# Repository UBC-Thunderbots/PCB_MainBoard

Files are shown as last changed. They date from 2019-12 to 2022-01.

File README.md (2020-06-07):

# PCB_MainBoard README

## Description

This repository contains Altium PCB files for UBC Thunderbots' main board pcb. Anyone who wishes to push changes to this project must get permission from the current Electrical Team Lead.

## Getting Started

### Required software

1. git
2. Altium Designer

### Instructions

1. Either create a new working branch or select an existing branch other than `master`.
2. **Recursively clone** (`git clone --recurse-submodules`) your working branch of the repository to your PC (i.e. `C:/Documents/thunderbots/PCB_MainBoard`).
3. In Altium Designer, navigate to *Preferences -> Data Management -> Version Control* and ensure **SVN - Subversion** is enabled and **Version 1.9** is selected.
4. In Altium Designer, navigate to *Preferences -> Data Management -> Design Repositories*.
5. Within *Design Repositories* click on on *Connect To* -> **SVN**.
6. In the dialogue box that comes up, fill in the following information:

Field|Selection/Input
---|---
Name|PCB_MainBoard
Default Checkout Path|location of local repository (i.e. `C:/Documents/thunderbots/PCB_MainBoard`)
Method|https
Server|github.com
Server Port|Default
Repository Subfolder|/UBC-Thunderbots/PCB_MainBoard
User Name|*your github login username*
Password|*your github login password*

7. Click **Test**.

After your repository is connected, you can add or remove files like a regular Altium Project folder and then commit and push your changes to the remote repository.

[Reference](https://forum.live.altium.com/#posts/235981/718003)

### Altium_Libraries Submodule Integration

To enforce component and board compatibility, the Altium_Libraries repository is integrated as a submodule. Before making changes to a project, **ensure that your local `Altium_Libraries/` submodule is current**. This can be done using `git submodule update` in git bash.

## Repository Structure

At the highest level, there should be the most up to date board revisions, (e.g.
`mainboard-v1.0/`), `archive/`, and `Altium_Libraries/`. Any previous versions should be placed in `archive/`. Every board revision directory should abide by the following structure:

```
<name-v#>/
├── doc/
│   ├── <name>.pdf
│   └── <name>.xslx or <name>.csv
├── pcb/
│   ├── guidelines/
│   ├── <name>.PrjPCB
│   ├── <name>.SchDoc
│   └── <name>.PcbDoc
└── sim/
```

### doc/

For documentation and relevant non-simulation and layout files. This includes PDFs of the design and bills of materials (`*.xlsx` or `.csv` format).

### pcb/

For any PCB design software files related to the schematic capture and PCB layout of board. This includes schematic and PCB layout guidelines (`guidelines/`).

### sim/

For any simulation files related to the PCB design here.

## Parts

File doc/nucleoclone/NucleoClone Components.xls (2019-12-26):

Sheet: Part List Report
Part List |  | Bill of Materials for Project [NucleoClone.PrjPcb] (No PCB Document Selected)
Source Data From: |  | NucleoClone.PrjPcb
Project: |  | NucleoClone.PrjPcb
Variant: |  | None
Report Date: | 12/19/2019 | 12:15 PM
Print Date: | 2019-12-19 | 12:15:50
Designator | Comment | LibRef | Footprint | Description
B1 | SW-PUSH-CMS | MCD-00002 | SWI_WEALTHMETAL_TD-0341_4P_BLUE | Non-Open Push-Button 0.1A 24V
B2 | SW-PUSH-CMS | MCD-00001 | SWI_WEALTHMETAL_TD-0341_4P_BLACK | Non-Open Push-Button 0.1A 24V BLACK
C38 | Capacitor | MCD-00006 | C0402 | Capacitor, MLCC, 100nF, 16V, X7R, 10%, 0402, T=0.5mm
C39 | Capacitor | MCD-01121 | C0603 | Capacitor, MLCC, 4.7µF, 10V, X5R, 20%, 0603, T=0,8mm
C40 | Capacitor | MCD-00097 | C0603 | Capacitor, MLCC, 4.7uF, 16V, X5R, 20%, 0603, T=0,8mm
C41 | Capacitor | MCD-00014 | C0805 | Capacitor, MLCC, 10uF, 25V, X5R, 10%, 0805, T=0,85mm
C42 | Capacitor | MCD-00014 | C0805 | Capacitor, MLCC, 10uF, 25V, X5R, 10%, 0805, T=0,85mm
C43 | Capacitor | MCD-00097 | C0603 | Capacitor, MLCC, 4.7uF, 16V, X5R, 20%, 0603, T=0,8mm
C44 | Capacitor | MCD-00237 | C0603 | Capacitor, MLCC, 100nF, 6V3, X5R, 10%, 0603, T=0,8mm
C45 | Capacitor | MCD-01121 | C0603 | Capacitor, MLCC, 4.7µF, 10V, X5R, 20%, 0603, T=0,8mm
C46 | Capacitor | MCD-01123 | C0402 | [obsolete] Capacitor, MLCC,100nF, 10V, X7R, 10%, 0402, T=0.5mm
C47 | Capacitor | MCD-01123 | C0402 | [obsolete] Capacitor, MLCC,100nF, 10V, X7R, 10%, 0402, T=0.5mm
C48 | Capacitor | MCD-00012 | C0603 | Capacitor, MLCC, 2.2uF, 10V, X5R, 10%, 0603, T=0,8mm
C49 | Capacitor | MCD-01123 | C0402 | [obsolete] Capacitor, MLCC,100nF, 10V, X7R, 10%, 0402, T=0.5mm
C50 | Capacitor | MCD-00012 | C0603 | Capacitor, MLCC, 2.2uF, 10V, X5R, 10%, 0603, T=0,8mm
C51 | Capacitor | MCD-01123 | C0402 | [obsolete] Capacitor, MLCC,100nF, 10V, X7R, 10%, 0402, T=0.5mm
C52 | Capacitor | MCD-01123 | C0402 | [obsolete] Capacitor, MLCC,100nF, 10V, X7R, 10%, 0402, T=0.5mm
C53 | Capacitor | MCD-01123 | C0402 | [obsolete] Capacitor, MLCC,100nF, 10V, X7R, 10%, 0402, T=0.5mm
C54 | Capacitor | MCD-01123 | C0402 | [obsolete] Capacitor, MLCC,100nF, 10V, X7R, 10%, 0402, T=0.5mm
C55 | Capacitor | MCD-01123 | C0402 | [obsolete] Capacitor, MLCC,100nF, 10V, X7R, 10%, 0402, T=0.5mm
C56 | Capacitor | MCD-01123 | C0402 | [obsolete] Capacitor, MLCC,100nF, 10V, X7R, 10%, 0402, T=0.5mm
C57 | Capacitor | MCD-01123 | C0402 | [obsolete] Capacitor, MLCC,100nF, 10V, X7R, 10%, 0402, T=0.5mm
C58 | Capacitor | MCD-01123 | C0402 | [obsolete] Capacitor, MLCC,100nF, 10V, X7R, 10%, 0402, T=0.5mm
C59 | Capacitor | MCD-00237 | C0603 | Capacitor, MLCC, 100nF, 6V3, X5R, 10%, 0603, T=0,8mm
C60 | Capacitor | MCD-01121 | C0603 | Capacitor, MLCC, 4.7µF, 10V, X5R, 20%, 0603, T=0,8mm
C61 | Capacitor | MCD-00238 | C0603 | Capacitor, MLCC, 1uF, 6V3, X5R, 10%, 0603, T=0,8mm
C62 | Capacitor | MCD-00006 | C0402 | Capacitor, MLCC, 100nF, 16V, X7R, 10%, 0402, T=0.5mm
C63 | Capacitor | MCD-00006 | C0402 | Capacitor, MLCC, 100nF, 16V, X7R, 10%, 0402, T=0.5mm
C64 | Capacitor | MCD-00238 | C0603 | Capacitor, MLCC, 1uF, 6V3, X5R, 10%, 0603, T=0,8mm
C65 | Capacitor | MCD-00237 | C0603 | Capacitor, MLCC, 100nF, 6V3, X5R, 10%, 0603, T=0,8mm
C66 | Capacitor | MCD-00238 | C0603 | Capacitor, MLCC, 1uF, 6V3, X5R, 10%, 0603, T=0,8mm
C67 | Capacitor | MCD-01123 | C0402 | [obsolete] Capacitor, MLCC,100nF, 10V, X7R, 10%, 0402, T=0.5mm
C68 | Capacitor | MCD-00237 | C0603 | Capacitor, MLCC, 100nF, 6V3, X5R, 10%, 0603, T=0,8mm
C69 | Capacitor | MCD-01374 | C0402 | Capacitor, MLCC, 5.6pF, 50V, NPO, 5%, 0402, T=0,5mm
C70 | Capacitor | MCD-01374 | C0402 | Capacitor, MLCC, 5.6pF, 50V, NPO, 5%, 0402, T=0,5mm
C71 | Capacitor | MCD-00003 | C0402 | Capacitor, MLCC, 5.1pF, 50V, NPO, +-0.25pF, 0402, T=0.5mm
C72 | Capacitor | MCD-00003 | C0402 | Capacitor, MLCC, 5.1pF, 50V, NPO, +-0.25pF, 0402, T=0.5mm
C84 | Capacitor | MCD-00009 | C0603 | Capacitor, MLCC, 4.7uF, 16V, X5R, 10%, 0603, T=0.8mm
CN11 | Header 35x2 | MCD-01210 | CON_SAMTEC_TSW-135-07-X-D | Header, 35x2, 2,54mm, VR, TH, Height 5.84mm/2.54mm
CN12 | Header 35x2 | MCD-01210 | CON_SAMTEC_TSW-135-07-X-D | Header, 35x2, 2,54mm, VR, TH, Height 5.84mm/2.54mm
CN13 | USB_uAB_47590.0001 | MCD-00661 | CON_USBMICROAB_MOLEX_47590-0001_H3 | USB-MICRO-AB Receptacle, RA, SMT + DIP, Standard, Top Mount, USB certified (symbol & footprint compatible with MCD-00022)
CN15 | Jumper_Header 2x1 | MCD-00214 | CON_SAMTEC_TSW-102-09-X-S | Header, 2x1, 2,54mm, VR, TH, Height 5.84mm/10.16mm
CN16 | Jumper_Header 2x1 | MCD-00214 | CON_SAMTEC_TSW-102-09-X-S | Header, 2x1, 2,54mm, VR, TH, Height 5.84mm/10.16mm
HW1 | Shunt Black 2.54mm | MCD-00043 |  | SHUNT 2.54mm BLACK
HW2 | Shunt Black 2.54mm | MCD-00043 |  | SHUNT 2.54mm BLACK
HW3 | Shunt Black 2.54mm | MCD-00043 |  | SHUNT 2.54mm BLACK
HW4 | Shunt Black 2.54mm | MCD-00043 |  | SHUNT 2.54mm BLACK
HW9 | BUTTON_HAT_BLUE | MCD-00634 |  | Blue Hat for switch TD0341X-G01-BLU
HW11 | BUTTON_HAT_BLACK | MCD-00635 |  | Black Hat for switch TD0341X-G01-BLA
HW12 | Shunt Black 2.54mm | MCD-00043 |  | SHUNT 2.54mm BLACK
HW13 | Shunt Black 2.54mm | MCD-00043 |  | SHUNT 2.54mm BLACK
JP2 | Jumper_Header 4x2 Fitted 1-2 | MCD-00686 | CON_SAMTEC_TSW-104-07-X-D | Header, 4x2, 2,54mm, VR, TH, Height 5.84mm/2.54mm - Shunt Fitted 1-2
JP4 | Jumper_Header 2x1 Fitted | MCD-00683 | CON_SAMTEC_TSW-102-07-G-S | Header, 2x1, 2,54mm, VR, TH, Height 5.84mm/2.54mm - Shunt Fitted by default
JP5 | Jumper_Header 3x1 Fitted 1-2 | MCD-00684 | CON_SAMTEC_TSW-103-07-F-S | Header, 3x1, 2,54mm, VR, TH, Height 5.84mm/2.54mm - Shunt Fitted 1-2 by default
LD1 | LED_green | MCD-00588 | LED_0603_OSRAM_LG-Q396-PS-35_GREEN_1A2K_H0P4 | LED Green, 0603 SMD, Forward Voltage Typ=2V, Max=2.5V
LD2 | LED_yellow | MCD-01061 | LED_0603_OSRAM_LY-Q396-P1Q2-36_YELLOW_1A2K_H0P4 | LED Yellow, 0603 SMD, Forward Voltage min=1.7V, Typ=2V, Max=2.3V
LD3 | LED_red | MCD-00586 | LED_0603_OSRAM_LS-Q976-NR-1_RED_1A2K_H0P8 | LED Red, 0603 SMD, Forward Voltage Typ=2V, Max=2.5V
LD5 | LED_green | MCD-00588 | LED_0603_OSRAM_LG-Q396-PS-35_GREEN_1A2K_H0P4 | LED Green, 0603 SMD, Forward Voltage Typ=2V, Max=2.5V
LD7 | LED_red | MCD-00587 | LED_0603_VISHAY_VLMS1300-GS08_RED_1A2K_H0P8 | LED Red, 0603 SMD, 2V Forward Voltage
LD8 | LED_green | MCD-00588 | LED_0603_OSRAM_LG-Q396-PS-35_GREEN_1A2K_H0P4 | LED Green, 0603 SMD, Forward Voltage Typ=2V, Max=2.5V
P? | Header 7X2 | Header 7X2 | HDR2X7 | Header, 7-Pin, Dual row
Q1 | 9013-SOT23 | MCD-00073 | NPN_SOT23 | NPN Bipolar Transistor
Q2 | 9013-SOT23 | MCD-00073 | NPN_SOT23 | NPN Bipolar Transistor
Q3 | 9013-SOT23 | MCD-00073 | NPN_SOT23 | NPN Bipolar Transistor
R12 | Resistor | MCD-00500 | R0603 | Resistor,620R,0603,1%,1/10W
R25 | Resistor | MCD-00053 | R0402 | Resistor,10K,0402,1%,1/16W
R26 | Resistor | MCD-00441 | R0402 | Resistor,270R,0402,1%,1/16W
R27 | Resistor | MCD-00441 | R0402 | Resistor,270R,0402,1%,1/16W
R28 | Resistor | MCD-00178 | R0402 | Resistor,470R,0402,1%,1/16W
R30 | Resistor | MCD-00053 | R0402 | Resistor,10K,0402,1%,1/16W
R31 | Resistor | MCD-00443 | R0402 | Resistor,27K,0402,1%,1/16W
R32 | Resistor | MCD-00493 | R0402 | Resistor,56K,0402,1%,1/16W
R33 | Resistor | MCD-00220 | R0603 | Resistor,10K,0603,1%,1/10W
R34 | Resistor | MCD-00220 | R0603 | Resistor,10K,0603,1%,1/10W
R35 | Resistor | MCD-00220 | R0603 | Resistor,10K,0603,1%,1/10W
R36 | Resistor | MCD-00056 | R0603 | Resistor,0R,0603,5%,1/10W
R37 | Resistor | MCD-00056 | R0603 | Resistor,0R,0603,5%,1/10W
R38 | Resistor | MCD-00056 | R0603 | Resistor,0R,0603,5%,1/10W
R39 | Resistor | MCD-00056 | R0603 | Resistor,0R,0603,5%,1/10W
R56 | Resistor | MCD-00063 | R0402 | Resistor,47K,0402,1%,1/16W
R60 | Resistor | MCD-00053 | R0402 | Resistor,10K,0402,1%,1/16W
R61 | Resistor | MCD-00063 | R0402 | Resistor,47K,0402,1%,1/16W
R62 | Resistor | MCD-00063 | R0402 | Resistor,47K,0402,1%,1/16W
R63 | Resistor | MCD-00053 | R0402 | Resistor,10K,0402,1%,1/16W
R64 | Resistor | MCD-00223 | R0603 | Resistor,100K,0603,1%,1/10W
R65 | Resistor | MCD-00461 | R0402 | Resistor,360R,0402,1%,1/16W
R66 | Resistor | MCD-00441 | R0402 | Resistor,270R,0402,1%,1/16W
R68 | Resistor | MCD-00223 | R0603 | Resistor,100K,0603,1%,1/10W
R69 | Resistor | MCD-00223 | R0603 | Resistor,100K,0603,1%,1/10W
R70 | Resistor | MCD-00223 | R0603 | Resistor,100K,0603,1%,1/10W
R71 | Resistor | MCD-00222 | R0603 | Resistor,47K,0603,1%,1/10W
R72 | Resistor | MCD-00222 | R0603 | Resistor,47K,0603,1%,1/10W
R73 | Resistor | MCD-00222 | R0603 | Resistor,47K,0603,1%,1/10W
R74 | Resistor | MCD-00197 | R0603 | Resistor,330R,0603,1%,1/10W
SB1 | SB_ON | MCD-00071 | SOLDER-BRIDGE_R0603-0R | Solder Bridge ON
SB2 | SB_ON | MCD-00071 | SOLDER-BRIDGE_R0603-0R | Solder Bridge ON
SB3 | SB_ON | MCD-00071 | SOLDER-BRIDGE_R0603-0R | Solder Bridge ON
SB4 | SB_ON | MCD-00071 | SOLDER-BRIDGE_R0603-0R | Solder Bridge ON
SB6 | SB_ON | MCD-00071 | SOLDER-BRIDGE_R0603-0R | Solder Bridge ON
SB8 | SB_ON | MCD-00071 | SOLDER-BRIDGE_R0603-0R | Solder Bridge ON
SB9 | SB_ON | MCD-00071 | SOLDER-BRIDGE_R0603-0R | Solder Bridge ON
SB10 | SB_ON | MCD-00071 | SOLDER-BRIDGE_R0603-0R | Solder Bridge ON
SB11 | SB_ON | MCD-00071 | SOLDER-BRIDGE_R0603-0R | Solder Bridge ON
SB12 | SB_ON | MCD-00071 | SOLDER-BRIDGE_R0603-0R | Solder Bridge ON
SB13 | SB_ON | MCD-00071 | SOLDER-BRIDGE_R0603-0R | Solder Bridge ON
SB14 | SB_ON | MCD-00071 | SOLDER-BRIDGE_R0603-0R | Solder Bridge ON
SB15 | SB_ON | MCD-00071 | SOLDER-BRIDGE_R0603-0R | Solder Bridge ON
SB16 | SB_ON | MCD-00071 | SOLDER-BRIDGE_R0603-0R | Solder Bridge ON
SB17 | SB_ON | MCD-00071 | SOLDER-BRIDGE_R0603-0R | Solder Bridge ON
SB18 | SB_ON | MCD-00071 | SOLDER-BRIDGE_R0603-0R | Solder Bridge ON
SB19 | SB_ON | MCD-00071 | SOLDER-BRIDGE_R0603-0R | Solder Bridge ON
SB20 | SB_ON | MCD-00071 | SOLDER-BRIDGE_R0603-0R | Solder Bridge ON
SB21 | SB_ON | MCD-00071 | SOLDER-BRIDGE_R0603-0R | Solder Bridge ON
SB22 | SB_ON | MCD-00071 | SOLDER-BRIDGE_R0603-0R | Solder Bridge ON
SB23 | SB_ON | MCD-00071 | SOLDER-BRIDGE_R0603-0R | Solder Bridge ON
SB24 | SB_ON | MCD-00071 | SOLDER-BRIDGE_R0603-0R | Solder Bridge ON
SB25 | SB_ON | MCD-00071 | SOLDER-BRIDGE_R0603-0R | Solder Bridge ON
SB34 | SB_ON | MCD-00071 | SOLDER-BRIDGE_R0603-0R | Solder Bridge ON
SB39 | SB_ON | MCD-00071 | SOLDER-BRIDGE_R0603-0R | Solder Bridge ON
SB40 | SB_ON | MCD-00071 | SOLDER-BRIDGE_R0603-0R | Solder Bridge ON
SB41 | SB_ON | MCD-00071 | SOLDER-BRIDGE_R0603-0R | Solder Bridge ON
SB42 | SB_ON | MCD-00071 | SOLDER-BRIDGE_R0603-0R | Solder Bridge ON
SB43 | SB_ON | MCD-00071 | SOLDER-BRIDGE_R0603-0R | Solder Bridge ON
SB44 | SB_ON | MCD-00071 | SOLDER-BRIDGE_R0603-0R | Solder Bridge ON
SB47 | SB_ON | MCD-00071 | SOLDER-BRIDGE_R0603-0R | Solder Bridge ON
SB51 | SB_ON | MCD-00071 | SOLDER-BRIDGE_R0603-0R | Solder Bridge ON
SB52 | SB_ON | MCD-00071 | SOLDER-BRIDGE_R0603-0R | Solder Bridge ON
SB56 | SB_ON | MCD-00071 | SOLDER-BRIDGE_R0603-0R | Solder Bridge ON
SB58 | SB_ON | MCD-00071 | SOLDER-BRIDGE_R0603-0R | Solder Bridge ON
SB66 | SB_ON | MCD-01618 | SOLDER-BRIDGE_R0402-0R | Solder Bridge 0402 ON
SB68 | SB_ON | MCD-01618 | SOLDER-BRIDGE_R0402-0R | Solder Bridge 0402 ON
SB76 | SB_ON | MCD-00071 | SOLDER-BRIDGE_R0603-0R | Solder Bridge ON
SB77 | SB_ON | MCD-00071 | SOLDER-BRIDGE_R0603-0R | Solder Bridge ON
SB80 | SB_ON | MCD-00071 | SOLDER-BRIDGE_R0603-0R | Solder Bridge ON
SB81 | SB_ON | MCD-01618 | SOLDER-BRIDGE_R0402-0R | Solder Bridge 0402 ON
SB82 | SB_ON | MCD-01618 | SOLDER-BRIDGE_R0402-0R | Solder Bridge 0402 ON
T1 | 9013-SOT23 | MCD-00073 | NPN_SOT23 | NPN Bipolar Transistor
U11 | ST1L05CPU33R | MCD-01025 | ICC_DFN6-EPAD_3X3_P095 | LDO, 3.3V, 1.3A, Very low quiescent current BiCMOS voltage regulator
U12 | LD1117S50TR | MCD-00088 | REG_SOT223-TAB | IC REG LDO 5V 0.8A SOT223
U13 | ST1L05BPUR | MCD-00581 | ICC_DFN6-EPAD_3X3_P095 | LDO Linear Voltage Regulator IC Positive Adjustable 1 Output Adjustable 1.3A 6-DFN (3x3)
U14 | STM32H7A3ZIT6 | MCD-01349 | ICC_LQFP144_20X20_P050_SOCKET_YAMAICHI_IC149-144-145-B5_NM | STM32H7A3ZIT6U, LQFP144 package, 20x20
U18 | STMPS2141STR | MCD-00083 | MOS_SOT23-5L | Enhanced single channel power switches with active low enable pin
U19 | USBLC6-2SC6 | MCD-00163 | ESD_SOT23-6L | Very low capacitance ESD protection
U20 | ESD-TRANSIL | MCD-00170 | ESD_ST0201 | ESD protection 6V1
U21 | ESD-TRANSIL | MCD-00251 | ESD_QFN2_1P6X1_P125 | High power transient voltage suppressor, 7V breakdown
U22 | ESD-TRANSIL | MCD-00170 | ESD_ST0201 | ESD protection 6V1
U23 | ESD-TRANSIL | MCD-00170 | ESD_ST0201 | ESD protection 6V1
X2 | XTAL_2_PINS | MCD-00091 | CRY_NX3215SA_2P | Crystal 32.768kHz, 6pF, +-20ppm, 50Kohms max, SMD
X3 | XTAL_4_PINS | MCD-01364 | CRY_NX2016SA_4P | Crystal 25MHz, 6pF, +-20ppm, 80ohms max, SMD

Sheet: All Data
Designator | Comment | Footprint | #Column Name Error:' Layer | #Column Name Error:' Rotation | #Column Name Error:' Height(Mil) | #Column Name Error:' Height(mm) | #Column Name Error:' Center-X(Mil) | #Column Name Error:' Center-X(mm) | #Column Name Error:' Center-Y(Mil) | #Column Name Error:' Center-Y(mm) | #Column Name Error:' Pad-X(Mil) | #Column Name Error:' Pad-X(mm) | #Column Name Error:' Pad-Y(Mil) | #Column Name Error:' Pad-Y(mm) | #Column Name Error:' Ref-X(Mil) | #Column Name Error:' Ref-X(mm) | #Column Name Error:' Ref-Y(Mil) | #Column Name Error:' Ref-Y(mm)
B1 | SW-PUSH-CMS | SWI_WEALTHMETAL_TD-0341_4P_BLUE
B2 | SW-PUSH-CMS | SWI_WEALTHMETAL_TD-0341_4P_BLACK
C38 | Capacitor | C0402
C39 | Capacitor | C0603
C40 | Capacitor | C0603
C41 | Capacitor | C0805
C42 | Capacitor | C0805
C43 | Capacitor | C0603
C44 | Capacitor | C0603
C45 | Capacitor | C0603
C46 | Capacitor | C0402
C47 | Capacitor | C0402
C48 | Capacitor | C0603
C49 | Capacitor | C0402
C50 | Capacitor | C0603
C51 | Capacitor | C0402
C52 | Capacitor | C0402
C53 | Capacitor | C0402
C54 | Capacitor | C0402
C55 | Capacitor | C0402
C56 | Capacitor | C0402
C57 | Capacitor | C0402
C58 | Capacitor | C0402
C59 | Capacitor | C0603
C60 | Capacitor | C0603
C61 | Capacitor | C0603
C62 | Capacitor | C0402
C63 | Capacitor | C0402
C64 | Capacitor | C0603
C65 | Capacitor | C0603
C66 | Capacitor | C0603
C67 | Capacitor | C0402
C68 | Capacitor | C0603
C69 | Capacitor | C0402
C70 | Capacitor | C0402
C71 | Capacitor | C0402
C72 | Capacitor | C0402
C84 | Capacitor | C0603
CN11 | Header 35x2 | CON_SAMTEC_TSW-135-07-X-D
CN12 | Header 35x2 | CON_SAMTEC_TSW-135-07-X-D
CN13 | USB_uAB_47590.0001 | CON_USBMICROAB_MOLEX_47590-0001_H3
CN15 | Jumper_Header 2x1 | CON_SAMTEC_TSW-102-09-X-S
CN16 | Jumper_Header 2x1 | CON_SAMTEC_TSW-102-09-X-S
HW1 | Shunt Black 2.54mm
HW2 | Shunt Black 2.54mm
HW3 | Shunt Black 2.54mm
HW4 | Shunt Black 2.54mm
HW9 | BUTTON_HAT_BLUE
HW11 | BUTTON_HAT_BLACK
HW12 | Shunt Black 2.54mm
HW13 | Shunt Black 2.54mm
JP2 | Jumper_Header 4x2 Fitted 1-2 | CON_SAMTEC_TSW-104-07-X-D
JP4 | Jumper_Header 2x1 Fitted | CON_SAMTEC_TSW-102-07-G-S
JP5 | Jumper_Header 3x1 Fitted 1-2 | CON_SAMTEC_TSW-103-07-F-S
LD1 | LED_green | LED_0603_OSRAM_LG-Q396-PS-35_GREEN_1A2K_H0P4
LD2 | LED_yellow | LED_0603_OSRAM_LY-Q396-P1Q2-36_YELLOW_1A2K_H0P4
LD3 | LED_red | LED_0603_OSRAM_LS-Q976-NR-1_RED_1A2K_H0P8
LD5 | LED_green | LED_0603_OSRAM_LG-Q396-PS-35_GREEN_1A2K_H0P4
LD7 | LED_red | LED_0603_VISHAY_VLMS1300-GS08_RED_1A2K_H0P8
LD8 | LED_green | LED_0603_OSRAM_LG-Q396-PS-35_GREEN_1A2K_H0P4
P? | Header 7X2 | HDR2X7
Q1 | 9013-SOT23 | NPN_SOT23
Q2 | 9013-SOT23 | NPN_SOT23
Q3 | 9013-SOT23 | NPN_SOT23
R12 | Resistor | R0603
R25 | Resistor | R0402
R26 | Resistor | R0402
R27 | Resistor | R0402
R28 | Resistor | R0402
R30 | Resistor | R0402
R31 | Resistor | R0402
R32 | Resistor | R0402
R33 | Resistor | R0603
R34 | Resistor | R0603
R35 | Resistor | R0603
R36 | Resistor | R0603
R37 | Resistor | R0603
R38 | Resistor | R0603
R39 | Resistor | R0603
R56 | Resistor | R0402
R60 | Resistor | R0402
R61 | Resistor | R0402
R62 | Resistor | R0402
R63 | Resistor | R0402
R64 | Resistor | R0603
R65 | Resistor | R0402
R66 | Resistor | R0402
R68 | Resistor | R0603
R69 | Resistor | R0603
R70 | Resistor | R0603
R71 | Resistor | R0603
R72 | Resistor | R0603
R73 | Resistor | R0603
R74 | Resistor | R0603
SB1 | SB_ON | SOLDER-BRIDGE_R0603-0R
SB2 | SB_ON | SOLDER-BRIDGE_R0603-0R
SB3 | SB_ON | SOLDER-BRIDGE_R0603-0R
SB4 | SB_ON | SOLDER-BRIDGE_R0603-0R
SB6 | SB_ON | SOLDER-BRIDGE_R0603-0R
SB8 | SB_ON | SOLDER-BRIDGE_R0603-0R
SB9 | SB_ON | SOLDER-BRIDGE_R0603-0R
SB10 | SB_ON | SOLDER-BRIDGE_R0603-0R
SB11 | SB_ON | SOLDER-BRIDGE_R0603-0R
SB12 | SB_ON | SOLDER-BRIDGE_R0603-0R
SB13 | SB_ON | SOLDER-BRIDGE_R0603-0R
SB14 | SB_ON | SOLDER-BRIDGE_R0603-0R
SB15 | SB_ON | SOLDER-BRIDGE_R0603-0R
SB16 | SB_ON | SOLDER-BRIDGE_R0603-0R
SB17 | SB_ON | SOLDER-BRIDGE_R0603-0R
SB18 | SB_ON | SOLDER-BRIDGE_R0603-0R
SB19 | SB_ON | SOLDER-BRIDGE_R0603-0R
SB20 | SB_ON | SOLDER-BRIDGE_R0603-0R
SB21 | SB_ON | SOLDER-BRIDGE_R0603-0R
SB22 | SB_ON | SOLDER-BRIDGE_R0603-0R
SB23 | SB_ON | SOLDER-BRIDGE_R0603-0R
SB24 | SB_ON | SOLDER-BRIDGE_R0603-0R
SB25 | SB_ON | SOLDER-BRIDGE_R0603-0R
SB34 | SB_ON | SOLDER-BRIDGE_R0603-0R
SB39 | SB_ON | SOLDER-BRIDGE_R0603-0R
SB40 | SB_ON | SOLDER-BRIDGE_R0603-0R
SB41 | SB_ON | SOLDER-BRIDGE_R0603-0R
SB42 | SB_ON | SOLDER-BRIDGE_R0603-0R
SB43 | SB_ON | SOLDER-BRIDGE_R0603-0R
SB44 | SB_ON | SOLDER-BRIDGE_R0603-0R
SB47 | SB_ON | SOLDER-BRIDGE_R0603-0R
SB51 | SB_ON | SOLDER-BRIDGE_R0603-0R
SB52 | SB_ON | SOLDER-BRIDGE_R0603-0R
SB56 | SB_ON | SOLDER-BRIDGE_R0603-0R
SB58 | SB_ON | SOLDER-BRIDGE_R0603-0R
SB66 | SB_ON | SOLDER-BRIDGE_R0402-0R
SB68 | SB_ON | SOLDER-BRIDGE_R0402-0R
SB76 | SB_ON | SOLDER-BRIDGE_R0603-0R
SB77 | SB_ON | SOLDER-BRIDGE_R0603-0R
SB80 | SB_ON | SOLDER-BRIDGE_R0603-0R
SB81 | SB_ON | SOLDER-BRIDGE_R0402-0R
SB82 | SB_ON | SOLDER-BRIDGE_R0402-0R
T1 | 9013-SOT23 | NPN_SOT23
U11 | ST1L05CPU33R | ICC_DFN6-EPAD_3X3_P095
U12 | LD1117S50TR | REG_SOT223-TAB
U13 | ST1L05BPUR | ICC_DFN6-EPAD_3X3_P095
U14 | STM32H7A3ZIT6 | ICC_LQFP144_20X20_P050_SOCKET_YAMAICHI_IC149-144-145-B5_NM
U18 | STMPS2141STR | MOS_SOT23-5L
U19 | USBLC6-2SC6 | ESD_SOT23-6L
U20 | ESD-TRANSIL | ESD_ST0201
U21 | ESD-TRANSIL | ESD_QFN2_1P6X1_P125
U22 | ESD-TRANSIL | ESD_ST0201
U23 | ESD-TRANSIL | ESD_ST0201
X2 | XTAL_2_PINS | CRY_NX3215SA_2P
X3 | XTAL_4_PINS | CRY_NX2016SA_4P

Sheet: Metric
Designator | Comment | Footprint | #Column Name Error:' Layer | #Column Name Error:' Rotation | #Column Name Error:' Center-X(mm) | #Column Name Error:' Center-Y(mm) | #Column Name Error:' Pad-X(mm) | #Column Name Error:' Pad-Y(mm) | #Column Name Error:' Ref-X(mm) | #Column Name Error:' Ref-Y(mm)
B1 | SW-PUSH-CMS | SWI_WEALTHMETAL_TD-0341_4P_BLUE
B2 | SW-PUSH-CMS | SWI_WEALTHMETAL_TD-0341_4P_BLACK
C38 | Capacitor | C0402
C39 | Capacitor | C0603
C40 | Capacitor | C0603
C41 | Capacitor | C0805
C42 | Capacitor | C0805
C43 | Capacitor | C0603
C44 | Capacitor | C0603
C45 | Capacitor | C0603
C46 | Capacitor | C0402
C47 | Capacitor | C0402
C48 | Capacitor | C0603
C49 | Capacitor | C0402
C50 | Capacitor | C0603
C51 | Capacitor | C0402
C52 | Capacitor | C0402
C53 | Capacitor | C0402
C54 | Capacitor | C0402
C55 | Capacitor | C0402
C56 | Capacitor | C0402
C57 | Capacitor | C0402
C58 | Capacitor | C0402
C59 | Capacitor | C0603
C60 | Capacitor | C0603
C61 | Capacitor | C0603
C62 | Capacitor | C0402
C63 | Capacitor | C0402
C64 | Capacitor | C0603
C65 | Capacitor | C0603
C66 | Capacitor | C0603
C67 | Capacitor | C0402
C68 | Capacitor | C0603
C69 | Capacitor | C0402
C70 | Capacitor | C0402
C71 | Capacitor | C0402
C72 | Capacitor | C0402
C84 | Capacitor | C0603
CN11 | Header 35x2 | CON_SAMTEC_TSW-135-07-X-D
CN12 | Header 35x2 | CON_SAMTEC_TSW-135-07-X-D
CN13 | USB_uAB_47590.0001 | CON_USBMICROAB_MOLEX_47590-0001_H3
CN15 | Jumper_Header 2x1 | CON_SAMTEC_TSW-102-09-X-S
CN16 | Jumper_Header 2x1 | CON_SAMTEC_TSW-102-09-X-S
HW1 | Shunt Black 2.54mm
HW2 | Shunt Black 2.54mm
HW3 | Shunt Black 2.54mm
HW4 | Shunt Black 2.54mm
HW9 | BUTTON_HAT_BLUE
HW11 | BUTTON_HAT_BLACK
HW12 | Shunt Black 2.54mm
HW13 | Shunt Black 2.54mm
JP2 | Jumper_Header 4x2 Fitted 1-2 | CON_SAMTEC_TSW-104-07-X-D
JP4 | Jumper_Header 2x1 Fitted | CON_SAMTEC_TSW-102-07-G-S
JP5 | Jumper_Header 3x1 Fitted 1-2 | CON_SAMTEC_TSW-103-07-F-S
LD1 | LED_green | LED_0603_OSRAM_LG-Q396-PS-35_GREEN_1A2K_H0P4
LD2 | LED_yellow | LED_0603_OSRAM_LY-Q396-P1Q2-36_YELLOW_1A2K_H0P4
LD3 | LED_red | LED_0603_OSRAM_LS-Q976-NR-1_RED_1A2K_H0P8
LD5 | LED_green | LED_0603_OSRAM_LG-Q396-PS-35_GREEN_1A2K_H0P4
LD7 | LED_red | LED_0603_VISHAY_VLMS1300-GS08_RED_1A2K_H0P8
LD8 | LED_green | LED_0603_OSRAM_LG-Q396-PS-35_GREEN_1A2K_H0P4
P? | Header 7X2 | HDR2X7
Q1 | 9013-SOT23 | NPN_SOT23
Q2 | 9013-SOT23 | NPN_SOT23
Q3 | 9013-SOT23 | NPN_SOT23
R12 | Resistor | R0603
R25 | Resistor | R0402
R26 | Resistor | R0402
R27 | Resistor | R0402
R28 | Resistor | R0402
R30 | Resistor | R0402
R31 | Resistor | R0402
R32 | Resistor | R0402
R33 | Resistor | R0603
R34 | Resistor | R0603
R35 | Resistor | R0603
R36 | Resistor | R0603
R37 | Resistor | R0603
R38 | Resistor | R0603
R39 | Resistor | R0603
R56 | Resistor | R0402
R60 | Resistor | R0402
R61 | Resistor | R0402
R62 | Resistor | R0402
R63 | Resistor | R0402
R64 | Resistor | R0603
R65 | Resistor | R0402
R66 | Resistor | R0402
R68 | Resistor | R0603
R69 | Resistor | R0603
R70 | Resistor | R0603
R71 | Resistor | R0603
R72 | Resistor | R0603
R73 | Resistor | R0603
R74 | Resistor | R0603
SB1 | SB_ON | SOLDER-BRIDGE_R0603-0R
SB2 | SB_ON | SOLDER-BRIDGE_R0603-0R
SB3 | SB_ON | SOLDER-BRIDGE_R0603-0R
SB4 | SB_ON | SOLDER-BRIDGE_R0603-0R
SB6 | SB_ON | SOLDER-BRIDGE_R0603-0R
SB8 | SB_ON | SOLDER-BRIDGE_R0603-0R
SB9 | SB_ON | SOLDER-BRIDGE_R0603-0R
SB10 | SB_ON | SOLDER-BRIDGE_R0603-0R
SB11 | SB_ON | SOLDER-BRIDGE_R0603-0R
SB12 | SB_ON | SOLDER-BRIDGE_R0603-0R
SB13 | SB_ON | SOLDER-BRIDGE_R0603-0R
SB14 | SB_ON | SOLDER-BRIDGE_R0603-0R
SB15 | SB_ON | SOLDER-BRIDGE_R0603-0R
SB16 | SB_ON | SOLDER-BRIDGE_R0603-0R
SB17 | SB_ON | SOLDER-BRIDGE_R0603-0R
SB18 | SB_ON | SOLDER-BRIDGE_R0603-0R
SB19 | SB_ON | SOLDER-BRIDGE_R0603-0R
SB20 | SB_ON | SOLDER-BRIDGE_R0603-0R
SB21 | SB_ON | SOLDER-BRIDGE_R0603-0R
SB22 | SB_ON | SOLDER-BRIDGE_R0603-0R
SB23 | SB_ON | SOLDER-BRIDGE_R0603-0R
SB24 | SB_ON | SOLDER-BRIDGE_R0603-0R
SB25 | SB_ON | SOLDER-BRIDGE_R0603-0R
SB34 | SB_ON | SOLDER-BRIDGE_R0603-0R
SB39 | SB_ON | SOLDER-BRIDGE_R0603-0R
SB40 | SB_ON | SOLDER-BRIDGE_R0603-0R
SB41 | SB_ON | SOLDER-BRIDGE_R0603-0R
SB42 | SB_ON | SOLDER-BRIDGE_R0603-0R
SB43 | SB_ON | SOLDER-BRIDGE_R0603-0R
SB44 | SB_ON | SOLDER-BRIDGE_R0603-0R
SB47 | SB_ON | SOLDER-BRIDGE_R0603-0R
SB51 | SB_ON | SOLDER-BRIDGE_R0603-0R
SB52 | SB_ON | SOLDER-BRIDGE_R0603-0R
SB56 | SB_ON | SOLDER-BRIDGE_R0603-0R
SB58 | SB_ON | SOLDER-BRIDGE_R0603-0R
SB66 | SB_ON | SOLDER-BRIDGE_R0402-0R
SB68 | SB_ON | SOLDER-BRIDGE_R0402-0R
SB76 | SB_ON | SOLDER-BRIDGE_R0603-0R
SB77 | SB_ON | SOLDER-BRIDGE_R0603-0R
SB80 | SB_ON | SOLDER-BRIDGE_R0603-0R
SB81 | SB_ON | SOLDER-BRIDGE_R0402-0R
SB82 | SB_ON | SOLDER-BRIDGE_R0402-0R
T1 | 9013-SOT23 | NPN_SOT23
U11 | ST1L05CPU33R | ICC_DFN6-EPAD_3X3_P095
U12 | LD1117S50TR | REG_SOT223-TAB
U13 | ST1L05BPUR | ICC_DFN6-EPAD_3X3_P095
U14 | STM32H7A3ZIT6 | ICC_LQFP144_20X20_P050_SOCKET_YAMAICHI_IC149-144-145-B5_NM
U18 | STMPS2141STR | MOS_SOT23-5L
U19 | USBLC6-2SC6 | ESD_SOT23-6L
U20 | ESD-TRANSIL | ESD_ST0201
U21 | ESD-TRANSIL | ESD_QFN2_1P6X1_P125
U22 | ESD-TRANSIL | ESD_ST0201
U23 | ESD-TRANSIL | ESD_ST0201
X2 | XTAL_2_PINS | CRY_NX3215SA_2P
X3 | XTAL_4_PINS | CRY_NX2016SA_4P

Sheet: Imperial
Designator | Comment | Footprint | #Column Name Error:' Layer | #Column Name Error:' Rotation | #Column Name Error:' Center-X(Mil) | #Column Name Error:' Center-Y(Mil) | #Column Name Error:' Pad-X(Mil) | #Column Name Error:' Pad-Y(Mil) | #Column Name Error:' Ref-X(Mil) | #Column Name Error:' Ref-Y(Mil)
B1 | SW-PUSH-CMS | SWI_WEALTHMETAL_TD-0341_4P_BLUE
B2 | SW-PUSH-CMS | SWI_WEALTHMETAL_TD-0341_4P_BLACK
C38 | Capacitor | C0402
C39 | Capacitor | C0603
C40 | Capacitor | C0603
C41 | Capacitor | C0805
C42 | Capacitor | C0805
C43 | Capacitor | C0603
C44 | Capacitor | C0603
C45 | Capacitor | C0603
C46 | Capacitor | C0402
C47 | Capacitor | C0402
C48 | Capacitor | C0603
C49 | Capacitor | C0402
C50 | Capacitor | C0603
C51 | Capacitor | C0402
C52 | Capacitor | C0402
C53 | Capacitor | C0402
C54 | Capacitor | C0402
C55 | Capacitor | C0402
C56 | Capacitor | C0402
C57 | Capacitor | C0402
C58 | Capacitor | C0402
C59 | Capacitor | C0603
C60 | Capacitor | C0603
C61 | Capacitor | C0603
C62 | Capacitor | C0402
C63 | Capacitor | C0402
C64 | Capacitor | C0603
C65 | Capacitor | C0603
C66 | Capacitor | C0603
C67 | Capacitor | C0402
C68 | Capacitor | C0603
C69 | Capacitor | C0402
C70 | Capacitor | C0402
C71 | Capacitor | C0402
C72 | Capacitor | C0402
C84 | Capacitor | C0603
CN11 | Header 35x2 | CON_SAMTEC_TSW-135-07-X-D
CN12 | Header 35x2 | CON_SAMTEC_TSW-135-07-X-D
CN13 | USB_uAB_47590.0001 | CON_USBMICROAB_MOLEX_47590-0001_H3
CN15 | Jumper_Header 2x1 | CON_SAMTEC_TSW-102-09-X-S
CN16 | Jumper_Header 2x1 | CON_SAMTEC_TSW-102-09-X-S
HW1 | Shunt Black 2.54mm
HW2 | Shunt Black 2.54mm
HW3 | Shunt Black 2.54mm
HW4 | Shunt Black 2.54mm
HW9 | BUTTON_HAT_BLUE
HW11 | BUTTON_HAT_BLACK
HW12 | Shunt Black 2.54mm
HW13 | Shunt Black 2.54mm
JP2 | Jumper_Header 4x2 Fitted 1-2 | CON_SAMTEC_TSW-104-07-X-D
JP4 | Jumper_Header 2x1 Fitted | CON_SAMTEC_TSW-102-07-G-S
JP5 | Jumper_Header 3x1 Fitted 1-2 | CON_SAMTEC_TSW-103-07-F-S
LD1 | LED_green | LED_0603_OSRAM_LG-Q396-PS-35_GREEN_1A2K_H0P4
LD2 | LED_yellow | LED_0603_OSRAM_LY-Q396-P1Q2-36_YELLOW_1A2K_H0P4
LD3 | LED_red | LED_0603_OSRAM_LS-Q976-NR-1_RED_1A2K_H0P8
LD5 | LED_green | LED_0603_OSRAM_LG-Q396-PS-35_GREEN_1A2K_H0P4
LD7 | LED_red | LED_0603_VISHAY_VLMS1300-GS08_RED_1A2K_H0P8
LD8 | LED_green | LED_0603_OSRAM_LG-Q396-PS-35_GREEN_1A2K_H0P4
P? | Header 7X2 | HDR2X7
Q1 | 9013-SOT23 | NPN_SOT23
Q2 | 9013-SOT23 | NPN_SOT23
Q3 | 9013-SOT23 | NPN_SOT23
R12 | Resistor | R0603
R25 | Resistor | R0402
R26 | Resistor | R0402
R27 | Resistor | R0402
R28 | Resistor | R0402
R30 | Resistor | R0402
R31 | Resistor | R0402
R32 | Resistor | R0402
R33 | Resistor | R0603
R34 | Resistor | R0603
R35 | Resistor | R0603
R36 | Resistor | R0603
R37 | Resistor | R0603
R38 | Resistor | R0603
R39 | Resistor | R0603
R56 | Resistor | R0402
R60 | Resistor | R0402
R61 | Resistor | R0402
R62 | Resistor | R0402
R63 | Resistor | R0402
R64 | Resistor | R0603
R65 | Resistor | R0402
R66 | Resistor | R0402
R68 | Resistor | R0603
R69 | Resistor | R0603
R70 | Resistor | R0603
R71 | Resistor | R0603
R72 | Resistor | R0603
R73 | Resistor | R0603
R74 | Resistor | R0603
SB1 | SB_ON | SOLDER-BRIDGE_R0603-0R
SB2 | SB_ON | SOLDER-BRIDGE_R0603-0R
SB3 | SB_ON | SOLDER-BRIDGE_R0603-0R
SB4 | SB_ON | SOLDER-BRIDGE_R0603-0R
SB6 | SB_ON | SOLDER-BRIDGE_R0603-0R
SB8 | SB_ON | SOLDER-BRIDGE_R0603-0R
SB9 | SB_ON | SOLDER-BRIDGE_R0603-0R
SB10 | SB_ON | SOLDER-BRIDGE_R0603-0R
SB11 | SB_ON | SOLDER-BRIDGE_R0603-0R
SB12 | SB_ON | SOLDER-BRIDGE_R0603-0R
SB13 | SB_ON | SOLDER-BRIDGE_R0603-0R
SB14 | SB_ON | SOLDER-BRIDGE_R0603-0R
SB15 | SB_ON | SOLDER-BRIDGE_R0603-0R
SB16 | SB_ON | SOLDER-BRIDGE_R0603-0R
SB17 | SB_ON | SOLDER-BRIDGE_R0603-0R
SB18 | SB_ON | SOLDER-BRIDGE_R0603-0R
SB19 | SB_ON | SOLDER-BRIDGE_R0603-0R
SB20 | SB_ON | SOLDER-BRIDGE_R0603-0R
SB21 | SB_ON | SOLDER-BRIDGE_R0603-0R
SB22 | SB_ON | SOLDER-BRIDGE_R0603-0R
SB23 | SB_ON | SOLDER-BRIDGE_R0603-0R
SB24 | SB_ON | SOLDER-BRIDGE_R0603-0R
SB25 | SB_ON | SOLDER-BRIDGE_R0603-0R
SB34 | SB_ON | SOLDER-BRIDGE_R0603-0R
SB39 | SB_ON | SOLDER-BRIDGE_R0603-0R
SB40 | SB_ON | SOLDER-BRIDGE_R0603-0R
SB41 | SB_ON | SOLDER-BRIDGE_R0603-0R
SB42 | SB_ON | SOLDER-BRIDGE_R0603-0R
SB43 | SB_ON | SOLDER-BRIDGE_R0603-0R
SB44 | SB_ON | SOLDER-BRIDGE_R0603-0R
SB47 | SB_ON | SOLDER-BRIDGE_R0603-0R
SB51 | SB_ON | SOLDER-BRIDGE_R0603-0R
SB52 | SB_ON | SOLDER-BRIDGE_R0603-0R
SB56 | SB_ON | SOLDER-BRIDGE_R0603-0R
SB58 | SB_ON | SOLDER-BRIDGE_R0603-0R
SB66 | SB_ON | SOLDER-BRIDGE_R0402-0R
SB68 | SB_ON | SOLDER-BRIDGE_R0402-0R
SB76 | SB_ON | SOLDER-BRIDGE_R0603-0R
SB77 | SB_ON | SOLDER-BRIDGE_R0603-0R
SB80 | SB_ON | SOLDER-BRIDGE_R0603-0R
SB81 | SB_ON | SOLDER-BRIDGE_R0402-0R
SB82 | SB_ON | SOLDER-BRIDGE_R0402-0R
T1 | 9013-SOT23 | NPN_SOT23
U11 | ST1L05CPU33R | ICC_DFN6-EPAD_3X3_P095
U12 | LD1117S50TR | REG_SOT223-TAB
U13 | ST1L05BPUR | ICC_DFN6-EPAD_3X3_P095
U14 | STM32H7A3ZIT6 | ICC_LQFP144_20X20_P050_SOCKET_YAMAICHI_IC149-144-145-B5_NM
U18 | STMPS2141STR | MOS_SOT23-5L
U19 | USBLC6-2SC6 | ESD_SOT23-6L
U20 | ESD-TRANSIL | ESD_ST0201
U21 | ESD-TRANSIL | ESD_QFN2_1P6X1_P125
U22 | ESD-TRANSIL | ESD_ST0201
U23 | ESD-TRANSIL | ESD_ST0201
X2 | XTAL_2_PINS | CRY_NX3215SA_2P
X3 | XTAL_4_PINS | CRY_NX2016SA_4P

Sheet: Project Information
Project Full Path | C:\Users\liamb\Documents\thunderbots\PCB_NucleoClone\NucleoClone.PrjPcb
Project Filename | NucleoClone.PrjPcb
Variant Name | None
Data-Source Filename | NucleoClone.PrjPcb
Data-Source Full Path | C:\Users\liamb\Documents\thunderbots\PCB_NucleoClone\NucleoClone.PrjPcb
Title | Bill of Materials for Project [NucleoClone.PrjPcb] (No PCB Document Selected)
Total Quantity | 149
Report Time | 12:15 PM
Report Date | 12/19/2019
Report Date & Tine | 12/19/2019 12:15 PM
Output Name | Bill of Materials
Output Type | BOM_PartType
Output Generator Name | BOM
Output Generator Description | Bill of Materials

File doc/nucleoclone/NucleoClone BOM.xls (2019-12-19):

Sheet: BOM Report
Bill of Materials |  |  | Bill of Materials for Variant [Thunderbots_Clone] of Project [NucleoClone.PrjPcb] (No PCB Document Selected)
Source Data From: |  | NucleoClone.PrjPcb
Project: |  | NucleoClone.PrjPcb
Variant: |  | Thunderbots_Clone
Creation Date: | 30/11/19 | 14:26
Print Date: | 2019-11-30 | 16:44:19
Footprint | Comment | LibRef | Designator | Description | Quantity
SWI_WEALTHMETAL_TD-0341_4P_BLUE | SW-PUSH-CMS | MCD-00002 | B1 | Non-Open Push-Button 0.1A 24V | 1
SWI_WEALTHMETAL_TD-0341_4P_BLACK | SW-PUSH-CMS | MCD-00001 | B2 | Non-Open Push-Button 0.1A 24V BLACK | 1
C0603 | Capacitor | MCD-00238, MCD-00237, MCD-00012, MCD-00010, MCD-00009, MCD-01121, MCD-00097, MCD-01124 | C1, C2, C3, C4, C7, C12, C13, C18, C23, C26, C27, C35, C36, C39, C40, C43, C44, C45, C48, C50, C59, C60, C61, C64, C65, C66, C68, C73, C78, C79, C80, C81, C82, C83, C84 | Capacitor, MLCC, 1uF, 6V3, X5R, 10%, 0603, T=0,8mm, Capacitor, MLCC, 100nF, 6V3, X5R, 10%, 0603, T=0,8mm, Capacitor, MLCC, 2.2uF, 10V, X5R, 10%, 0603, T=0,8mm, Capacitor, MLCC, 1uF, 16V, X5R, 10%, 0603, T=0,8mm, Capacitor, MLCC, 4.7uF, 16V, X5R, 10%, 0603, T=0.8mm, Capacitor, MLCC, 4.7µF, 10V, X5R, 20%, 0603, T=0,8mm, Capacitor, MLCC, 4.7uF, 16V, X5R, 20%, 0603, T=0,8mm, Capacitor, MLCC, 10µF, 10V, X5R, 10%, 0603, T=0.8mm | 35
C0402 | Capacitor | MCD-00016, MCD-00205, MCD-00102, MCD-00011, MCD-00006, MCD-01123, MCD-01374, MCD-00003, MCD-00095, MCD-00724 | C5, C6, C8, C9, C10, C11, C14, C15, C16, C17, C19, C20, C21, C22, C24, C25, C28, C29, C30, C31, C32, C33, C34, C37, C38, C46, C47, C49, C51, C52, C53, C54, C55, C56, C57, C58, C62, C63, C67, C69, C70, C71, C72, C74, C75, C76, C77 | Capacitor, MLCC, 20pF, 50V, NPO, 5%, 0402, T=0,5mm, Capacitor, MLCC, 100pF, 50V, NPO, 5%, 0402, T=0,5mm, Capacitor, MLCC, 100nF, 16V, X7R, 10%, 0402, T=0,5mm, Capacitor, MLCC, 10nF, 16V, X7R, 10%, 0402, T=0.5mm, Capacitor, MLCC, 100nF, 16V, X7R, 10%, 0402, T=0.5mm, [obsolete] Capacitor, MLCC,100nF, 10V, X7R, 10%, 0402, T=0.5mm, Capacitor, MLCC, 5.6pF, 50V, NPO, 5%, 0402, T=0,5mm, Capacitor, MLCC, 5.1pF, 50V, NPO, +-0.25pF, 0402, T=0.5mm, Capacitor, MLCC, 1uF, 6V3, X5R, 10%, 0402, T=0,5mm, Capacitor, MLCC, 470pF, 50V, NPO, 5%, 0402, T=0,5mm | 47
C0805 | Capacitor | MCD-00014 | C41, C42 | Capacitor, MLCC, 10uF, 25V, X5R, 10%, 0805, T=0,85mm | 2
C1206_H1P6 | Capacitor | MCD-00722 | C85 | Capacitor, MLCC, 1nF, 2KV, X7R, 10%, 1206, T=1,25mm | 1
CON_USBMICROB_MOLEX_105017-0001_H2P90 | USB_uB_105017.0001 | MCD-00028 | CN1 | USB-MICRO-B, 0.65mm, RA, SMT, Bottom Mount, | 1
CON_SAMTEC_TSW-104-07-G-S | Header 4x1 | MCD-00029 | CN2 | Header, 4x1, 2,54mm, VR, TH, Height 5.84mm/2.54mm | 1
CON_SAMTEC_TSW-102-09-X-S | Jumper_Header 2x1 | MCD-00214 | CN3, CN4, CN15, CN16 | Header, 2x1, 2,54mm, VR, TH, Height 5.84mm/10.16mm | 4
CON_STDC14_Receiver_MEDIUM_WITH_MIPI10_3D | Header 7x2 | MCD-01226 | CN5 | Header 5x2, 1.27mm, Dual row, Straight, Surface mount, vertical male connector. 3.05mm lead. Mates with FFSD connector. Footprint compatible with FTSH-107-01-L-DV,-K,-A,-P,-ES (STDC14 MEDIUM) | 1
CON_SAMTEC_SSW-110-23-X-D_N144_ARD | Socket 10x2_N144_ARD | MCD-01039 | CN7 | Socket, 10x2, 2.54mm, VR, TH, Height 8.51mm/10mm, Low insertion force. | 1
CON_SAMTEC_SSW-108-23-X-D_N144_ARD | Socket 8x2_N144_ARD | MCD-01037 | CN8 | Socket, 8x2, 2.54mm, VR, TH, Height 8.51mm/10mm, Low insertion force. | 1
CON_SAMTEC_SSW-115-23-X-D_N144_ARD | Socket 15x2_N144_ARD | MCD-01040 | CN9 | Socket, 15x2, 2.54mm, VR, TH, Height 8.51mm/10mm, Low insertion force. | 1
CON_SAMTEC_SSW-117-23-X-D_N144_ARD | Socket 17x2_N144_ARD | MCD-01041 | CN10 | Socket, 17x2, 2.54mm, VR, TH, Height 8.51mm/10mm, Low insertion force | 1
CON_SAMTEC_TSW-135-07-X-D | Header 35x2 | MCD-01210 | CN11, CN12 | Header, 35x2, 2,54mm, VR, TH, Height 5.84mm/2.54mm | 2
CON_USBMICROAB_MOLEX_47590-0001_H3 | USB_uAB_47590.0001 | MCD-00661 | CN13 | USB-MICRO-AB Receptacle, RA, SMT + DIP, Standard, Top Mount, USB certified (symbol & footprint compatible with MCD-00022) | 1
CON_RJ45_DGKYD_KRJ-CB4.2GYZNL | RJ45_KRJ-CB4.2GYZNL | MCD-00717 | CN14 | RJ45 jack, single port, with LEDS, Metal shielded dip low profile | 1
DIO_SOD323 | BAT60JFILM | MCD-00034 | D1, D2, D3 | BAT60JFILM | 3
 | Shunt Black 2.54mm | MCD-00043 | HW1, HW2, HW3, HW4, HW6, HW7, HW8, HW12, HW13 | SHUNT 2.54mm BLACK | 9
 | BUTTON_HAT_BLUE | MCD-00634 | HW9 | Blue Hat for switch TD0341X-G01-BLU | 1
 | BUTTON_HAT_BLACK | MCD-00635 | HW11 | Black Hat for switch TD0341X-G01-BLA | 1
CON_SAMTEC_TSW-102-07-G-S | Jumper_Header 2x1 | MCD-00045 | JP1 | Header, 2x1, 2,54mm, VR, TH, Height 5.84mm/2.54mm | 1
CON_SAMTEC_TSW-104-07-X-D | Jumper_Header 4x2 Fitted 1-2 | MCD-00686 | JP2 | Header, 4x2, 2,54mm, VR, TH, Height 5.84mm/2.54mm - Shunt Fitted 1-2 | 1
CON_SAMTEC_TSW-102-07-G-S | Jumper_Header 2x1 Fitted | MCD-00683 | JP3, JP4, JP6 | Header, 2x1, 2,54mm, VR, TH, Height 5.84mm/2.54mm - Shunt Fitted by default | 3
CON_SAMTEC_TSW-103-07-F-S | Jumper_Header 3x1 Fitted 1-2 | MCD-00684 | JP5 | Header, 3x1, 2,54mm, VR, TH, Height 5.84mm/2.54mm - Shunt Fitted 1-2 by default | 1
L0603 | BEAD | MCD-00047 | L1 | SMD Chip ferrite bead, 600R@100MHz +/-25%, 350mA, 500mohm DC, 0603, T=0.8mm | 1
LED_0603_OSRAM_LG-Q396-PS-35_GREEN_1A2K_H0P4 | LED_green | MCD-00588 | LD1, LD5, LD8 | LED Green, 0603 SMD, Forward Voltage Typ=2V, Max=2.5V | 3
LED_0603_OSRAM_LY-Q396-P1Q2-36_YELLOW_1A2K_H0P4 | LED_yellow | MCD-01061 | LD2 | LED Yellow, 0603 SMD, Forward Voltage min=1.7V, Typ=2V, Max=2.3V | 1
LED_0603_OSRAM_LS-Q976-NR-1_RED_1A2K_H0P8 | LED_red | MCD-00586 | LD3 | LED Red, 0603 SMD, Forward Voltage Typ=2V, Max=2.5V | 1
LED_BI-GR_HSMF-A201-A00J1 | LD_BICOLOR_CMS | MCD-00051 | LD4 | LED Bicolor | 1
LED_0603_RED | LED_red | MCD-00049 | LD6 | LED, Red, 0603 | 1
LED_0603_VISHAY_VLMS1300-GS08_RED_1A2K_H0P8 | LED_red | MCD-00587 | LD7 | LED Red, 0603 SMD, 2V Forward Voltage | 1
NPN_SOT23 | 9013-SOT23 | MCD-00073 | Q1, Q2, Q3, T1 | NPN Bipolar Transistor | 4
R0603 | Resistor | MCD-00223, MCD-00070, MCD-00220, MCD-00197, MCD-00500, MCD-00056, MCD-00222 | R1, R2, R4, R7, R8, R9, R12, R33, R34, R35, R36, R37, R38, R39, R64, R68, R69, R70, R71, R72, R73, R74 | Resistor,100K,0603,1%,1/10W, Resistor,1K,0603,1%,1/10W, Resistor,10K,0603,1%,1/10W, Resistor,330R,0603,1%,1/10W, Resistor,620R,0603,1%,1/10W, Resistor,0R,0603,5%,1/10W, Resistor,47K,0603,1%,1/10W | 22
R0402 | Resistor | MCD-00189, MCD-00119, MCD-00185, MCD-00065, MCD-00055, MCD-00053, MCD-00441, MCD-00178, MCD-00443, MCD-00493, MCD-00455, MCD-00068, MCD-00052, MCD-00723, MCD-00515, MCD-00063, MCD-00461, MCD-00565 | R3, R5, R6, R10, R11, R13, R14, R15, R17, R18, R20, R21, R22, R23, R24, R25, R26, R27, R28, R29, R30, R31, R32, R40, R41, R42, R43, R44, R45, R46, R47, R48, R49, R50, R51, R52, R53, R54, R55, R56, R57, R58, R59, R60, R61, R62, R63, R65, R66, R67, R75, R76, R77, R78 | Resistor,22R,0402,1%,1/16W, Resistor,100R,0402,1%,1/16W, Resistor,3K,0402,1%,1/16W, Resistor,4K7,0402,1%,1/16W, Resistor,2K7,0402,1%,1/16W, Resistor,10K,0402,1%,1/16W, Resistor,270R,0402,1%,1/16W, Resistor,470R,0402,1%,1/16W, Resistor,27K,0402,1%,1/16W, Resistor,56K,0402,1%,1/16W, Resistor,33R,0402,1%,1/16W, Resistor,1K5,0402,1%,1/16W, Resistor,0R,0402,5%,1/16W, Resistor,12K1,0402,1%,1/16W, Resistor,75R,0402,1%,1/16W, Resistor,47K,0402,1%,1/16W, Resistor,360R,0402,1%,1/16W, Resistor,49R9,0402,1%,1/16W | 54
SOLDER-BRIDGE_R0603-0R | SB_ON | MCD-00071 | SB1, SB2, SB3, SB4, SB5, SB6, SB7, SB8, SB9, SB10, SB11, SB12, SB13, SB14, SB15, SB16, SB17, SB18, SB19, SB20, SB21, SB22, SB23, SB24, SB25, SB26, SB27, SB29, SB30, SB31, SB32, SB33, SB34, SB35, SB36, SB39, SB40, SB41, SB42, SB43, SB44, SB45, SB46, SB47, SB51, SB52, SB56, SB57, SB58, SB64, SB72, SB74, SB76, SB77, SB78, SB79, SB80 | Solder Bridge ON | 57
SOLDER-BRIDGE_R0402-0R | SB_ON | MCD-01618 | SB28, SB37, SB38, SB48, SB49, SB50, SB53, SB54, SB55, SB59, SB60, SB61, SB62, SB63, SB65, SB66, SB67, SB68, SB69, SB70, SB71, SB73, SB75, SB81, SB82 | Solder Bridge 0402 ON | 25
ICC_VSSOP8_DCU_R-PDSO-G8_2X2P30_P050 | SN74LVC2T45DCUT | MCD-00264 | U1, U10 | Dual bit dual supply bus transceiver | 2
MOS_SOT23-5L | STMPS2151STR | MCD-00159 | U2 | 500mA, Enhanced single channel power switches with active high enable pin | 1
ESD_ST0201 | ESD-TRANSIL | MCD-00170 | U3, U4, U20, U22, U23 | ESD protection 6V1 | 5
ESD_QFN-6L_1P7X1P5_P050 | ECMF02-2AMX6 | MCD-00649 | U5 | Common mode filter with ESD protection for USB 2.0 interface | 1
ESD_QFN2_1P6X1_P125 | ESD-TRANSIL | MCD-00251 | U6, U21 | High power transient voltage suppressor, 7V breakdown | 2
ICC_UFBGA201_176+25_10X10_P065 | ST-LINKV3E_SWD | MCD-00596 | U7 | STM32F723IEK (STM32F7) BGA176 | 1
ESD_SOT323-5L | ESDALC6V1W5 | MCD-00136 | U8, U24 | Dual Transil array for ESD protection | 2
REG_SOT23-5L | LD3985M33R | MCD-00086 | U9 | Ultra low drop-low noise BiCMOS voltage, regulators low ESR capacitors compatible | 1
ICC_DFN6-EPAD_3X3_P095 | ST1L05CPU33R | MCD-01025 | U11 | LDO, 3.3V, 1.3A, Very low quiescent current BiCMOS voltage regulator | 1
REG_SOT223-TAB | LD1117S50TR | MCD-00088 | U12 | IC REG LDO 5V 0.8A SOT223 | 1
ICC_DFN6-EPAD_3X3_P095 | ST1L05BPUR | MCD-00581 | U13 | LDO Linear Voltage Regulator IC Positive Adjustable 1 Output Adjustable 1.3A 6-DFN (3x3) | 1
ICC_LQFP144_20X20_P050_SOCKET_YAMAICHI_IC149-144-145-B5_NM | STM32H7A3ZIT6 | MCD-01349 | U14 | STM32H7A3ZIT6U, LQFP144 package, 20x20 | 1
ICC_VQFN24-EPAD_4X4_P050 | LAN8742A-CZ-TR | MCD-00719 | U15 | 10/100M RMII Ethernet transceiver | 1
ESD_SOT23-6L | USBLC6-4SC6 | MCD-00250 | U16 | Very low capacitance ESD protection , 4 lines | 1
TRS_DGKYD_KMS-1102NL | KMS-1102NL | MCD-00718 | U17 | Discrete Magnetic Transformer Module, 16 pins, SMT, 100 Base-TX | 1
MOS_SOT23-5L | STMPS2141STR | MCD-00083 | U18 | Enhanced single channel power switches with active low enable pin | 1
ESD_SOT23-6L | USBLC6-2SC6 | MCD-00163 | U19 | Very low capacitance ESD protection | 1
OSC_NDK_NZ2520SB_4P | OSCILLATOR_4_PINS | MCD-00597 | X1 | Oscillator 25Mhz, +-50ppm, Vcc:3.3V typ, square wave: [0.1Vcc;0.9Vcc], Enable pin, SMD | 1
CRY_NX3215SA_2P | XTAL_2_PINS | MCD-00091 | X2 | Crystal 32.768kHz, 6pF, +-20ppm, 50Kohms max, SMD | 1
CRY_NX2016SA_4P | XTAL_4_PINS | MCD-01364 | X3, X4 | Crystal 25MHz, 6pF, +-20ppm, 80ohms max, SMD | 2
 |  |  |  |  | 321
Approved |  | Notes

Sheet: Thunderbots Components
Default |  |  | Thunderbots Variant
Footprint | Description | Integrated Library Design Item ID | Package | Description | Source Link
SWI_WEALTHMETAL_TD-0341_4P_BLUE | Non-Open Push-Button 0.1A 24V
SWI_WEALTHMETAL_TD-0341_4P_BLACK | Non-Open Push-Button 0.1A 24V BLACK
C0603 | Capacitor, MLCC, 1uF, 6V3, X5R, 10%, 0603, T=0,8mm | CAP 1uF 0805
C0603 | Capacitor, MLCC, 100nF, 6V3, X5R, 10%, 0603, T=0,8mm | CAP 100nF 0805
C0603 | Capacitor, MLCC, 2.2uF, 10V, X5R, 10%, 0603, T=0,8mm | CAP 2.2uF 0805
C0603 | Capacitor, MLCC, 1uF, 16V, X5R, 10%, 0603, T=0,8mm | CAP 1uF 0805
C0603 | Capacitor, MLCC, 4.7uF, 16V, X5R, 10%, 0603, T=0.8mm | CAP 470pF 0805
C0603 | Capacitor, MLCC, 4.7µF, 10V, X5R, 20%, 0603, T=0,8mm | CAP 470pF 0805
C0603 | Capacitor, MLCC, 4.7uF, 16V, X5R, 20%, 0603, T=0,8mm | CAP 470pF 0805
C0603 | Capacitor, MLCC, 10µF, 10V, X5R, 10%, 0603, T=0.8mm |  | 1210 | 10µF ±10% 50V Ceramic Capacitor X7R 1210 (3225 Metric) | https://www.digikey.ca/product-detail/en/samsung-electro-mechanics/CL32B106KBJNNWE/1276-3388-2-ND/3889046
C0402 | Capacitor, MLCC, 20pF, 50V, NPO, 5%, 0402, T=0.5mm |  | 0805 | 20pF ±10% 50V Ceramic Capacitor C0G, NP0 0805 (2012 Metric) | https://www.digikey.ca/product-detail/en/avx-corporation/08055A200KAT2A/478-11887-1-ND/8573523
C0402 | Capacitor, MLCC, 100pF, 50V, NPO, 5%, 0402, T=0.5mm |  | 0805 | 100pF ±10% 50V Ceramic Capacitor C0G, NP0 0805 (2012 Metric) | https://www.digikey.ca/product-detail/en/kemet/C0805C101K5GACTU/399-1121-1-ND/411396
C0402 | Capacitor, MLCC, 100nF, 16V, X7R, 10%, 0402, T=0.5mm | CAP 100nF 0805
C0402 | Capacitor, MLCC, 10nF, 16V, X7R, 10%, 0402, T=0.5mm
C0402 | Capacitor, MLCC, 100nF, 16V, X7R, 10%, 0402, T=0.5mm | CAP 100nF 0805
C0402 | Capacitor, MLCC,100nF, 10V, X7R, 10%, 0402, T=0.5mm, | CAP 100nF 0805
C0402 | Capacitor, MLCC, 5.6pF, 50V, NPO, 5%, 0402, T=0.5mm,
C0402 | Capacitor, MLCC, 5.1pF, 50V, NPO, +-0.25pF, 0402, T=0.5mm
C0402 | Capacitor, MLCC, 1uF, 6V3, X5R, 10%, 0402, T=0.5mm
C0402 | Capacitor, MLCC, 470pF, 50V, NPO, 5%, 0402, T=0.5mm
C0805 | Capacitor, MLCC, 10uF, 25V, X5R, 10%, 0805, T=0,85mm
C1206_H1P6 | Capacitor, MLCC, 1nF, 2KV, X7R, 10%, 1206, T=1,25mm
CON_USBMICROB_MOLEX_105017-0001_H2P90 | USB-MICRO-B, 0.65mm, RA, SMT, Bottom Mount,
CON_SAMTEC_TSW-104-07-G-S | Header, 4x1, 2,54mm, VR, TH, Height 5.84mm/2.54mm
CON_SAMTEC_TSW-102-09-X-S | Header, 2x1, 2,54mm, VR, TH, Height 5.84mm/10.16mm
CON_STDC14_Receiver_MEDIUM_WITH_MIPI10_3D | Header 5x2, 1.27mm, Dual row, Straight, Surface mount, vertical male connector. 3.05mm lead. Mates with FFSD connector. Footprint compatible with FTSH-107-01-L-DV,-K,-A,-P,-ES (STDC14 MEDIUM)
CON_SAMTEC_SSW-110-23-X-D_N144_ARD | Socket, 10x2, 2.54mm, VR, TH, Height 8.51mm/10mm, Low insertion force.
CON_SAMTEC_SSW-108-23-X-D_N144_ARD | Socket, 8x2, 2.54mm, VR, TH, Height 8.51mm/10mm, Low insertion force.
CON_SAMTEC_SSW-115-23-X-D_N144_ARD | Socket, 15x2, 2.54mm, VR, TH, Height 8.51mm/10mm, Low insertion force.
CON_SAMTEC_SSW-117-23-X-D_N144_ARD | Socket, 17x2, 2.54mm, VR, TH, Height 8.51mm/10mm, Low insertion force
CON_SAMTEC_TSW-135-07-X-D | Header, 35x2, 2,54mm, VR, TH, Height 5.84mm/2.54mm
CON_USBMICROAB_MOLEX_47590-0001_H3 | USB-MICRO-AB Receptacle, RA, SMT + DIP, Standard, Top Mount, USB certified (symbol & footprint compatible with MCD-00022)
CON_RJ45_DGKYD_KRJ-CB4.2GYZNL | RJ45 jack, single port, with LEDS, Metal shielded dip low profile
DIO_SOD323 | BAT60JFILM
 | SHUNT 2.54mm BLACK
 | Blue Hat for switch TD0341X-G01-BLU
 | Black Hat for switch TD0341X-G01-BLA
CON_SAMTEC_TSW-102-07-G-S | Header, 2x1, 2,54mm, VR, TH, Height 5.84mm/2.54mm
CON_SAMTEC_TSW-104-07-X-D | Header, 4x2, 2,54mm, VR, TH, Height 5.84mm/2.54mm - Shunt Fitted 1-2
CON_SAMTEC_TSW-102-07-G-S | Header, 2x1, 2,54mm, VR, TH, Height 5.84mm/2.54mm - Shunt Fitted by default
CON_SAMTEC_TSW-103-07-F-S | Header, 3x1, 2,54mm, VR, TH, Height 5.84mm/2.54mm - Shunt Fitted 1-2 by default
L0603 | SMD Chip ferrite bead, 600R@100MHz +/-25%, 350mA, 500mohm DC, 0603, T=0.8mm
LED_0603_OSRAM_LG-Q396-PS-35_GREEN_1A2K_H0P4 | LED Green, 0603 SMD, Forward Voltage Typ=2V, Max=2.5V
LED_0603_OSRAM_LY-Q396-P1Q2-36_YELLOW_1A2K_H0P4 | LED Yellow, 0603 SMD, Forward Voltage min=1.7V, Typ=2V, Max=2.3V
LED_0603_OSRAM_LS-Q976-NR-1_RED_1A2K_H0P8 | LED Red, 0603 SMD, Forward Voltage Typ=2V, Max=2.5V
LED_BI-GR_HSMF-A201-A00J1 | LED Bicolor
LED_0603_RED | LED, Red, 0603
LED_0603_VISHAY_VLMS1300-GS08_RED_1A2K_H0P8 | LED Red, 0603 SMD, 2V Forward Voltage
NPN_SOT23 | NPN Bipolar Transistor
R0603 | Resistor,100K,0603,1%,1/10W
R0603 | Resistor,1K,0603,1%,1/10W
R0603 | Resistor,10K,0603,1%,1/10W
R0603 | Resistor,330R,0603,1%,1/10W
R0603 | Resistor,620R,0603,1%,1/10W
R0603 | Resistor,0R,0603,5%,1/10W
R0603 | Resistor,47K,0603,1%,1/10W
R0402 | Resistor,22R,0402,1%,1/16W,
R0402 | Resistor,100R,0402,1%,1/16W,
R0402 | Resistor,3K,0402,1%,1/16W,
R0402 | Resistor,4K7,0402,1%,1/16W,
R0402 | Resistor,2K7,0402,1%,1/16W,
R0402 | Resistor,10K,0402,1%,1/16W,
R0402 | Resistor,270R,0402,1%,1/16W,
R0402 | Resistor,470R,0402,1%,1/16W,
R0402 | Resistor,27K,0402,1%,1/16W,
R0402 | Resistor,56K,0402,1%,1/16W,
R0402 | Resistor,33R,0402,1%,1/16W,
R0402 | Resistor,1K5,0402,1%,1/16W,
R0402 | Resistor,0R,0402,5%,1/16W,
R0402 | Resistor,12K1,0402,1%,1/16W,
R0402 | Resistor,75R,0402,1%,1/16W,
R0402 | Resistor,47K,0402,1%,1/16W,
R0402 | Resistor,360R,0402,1%,1/16W,
R0402 | Resistor,49R9,0402,1%,1/16W
SOLDER-BRIDGE_R0603-0R | Solder Bridge ON
SOLDER-BRIDGE_R0402-0R | Solder Bridge 0402 ON
ICC_VSSOP8_DCU_R-PDSO-G8_2X2P30_P050 | Dual bit dual supply bus transceiver
MOS_SOT23-5L | 500mA, Enhanced single channel power switches with active high enable pin
ESD_ST0201 | ESD protection 6V1
ESD_QFN-6L_1P7X1P5_P050 | Common mode filter with ESD protection for USB 2.0 interface
ESD_QFN2_1P6X1_P125 | High power transient voltage suppressor, 7V breakdown
ICC_UFBGA201_176+25_10X10_P065 | STM32F723IEK (STM32F7) BGA176
ESD_SOT323-5L | Dual Transil array for ESD protection
REG_SOT23-5L | Ultra low drop-low noise BiCMOS voltage, regulators low ESR capacitors compatible
ICC_DFN6-EPAD_3X3_P095 | LDO, 3.3V, 1.3A, Very low quiescent current BiCMOS voltage regulator
REG_SOT223-TAB | IC REG LDO 5V 0.8A SOT223
ICC_DFN6-EPAD_3X3_P095 | LDO Linear Voltage Regulator IC Positive Adjustable 1 Output Adjustable 1.3A 6-DFN (3x3)
ICC_LQFP144_20X20_P050_SOCKET_YAMAICHI_IC149-144-145-B5_NM | STM32H7A3ZIT6U, LQFP144 package, 20x20
ICC_VQFN24-EPAD_4X4_P050 | 10/100M RMII Ethernet transceiver
ESD_SOT23-6L | Very low capacitance ESD protection , 4 lines
TRS_DGKYD_KMS-1102NL | Discrete Magnetic Transformer Module, 16 pins, SMT, 100 Base-TX
MOS_SOT23-5L | Enhanced single channel power switches with active low enable pin
ESD_SOT23-6L | Very low capacitance ESD protection
OSC_NDK_NZ2520SB_4P | Oscillator 25Mhz, +-50ppm, Vcc:3.3V typ, square wave: [0.1Vcc;0.9Vcc], Enable pin, SMD
CRY_NX3215SA_2P | Crystal 32.768kHz, 6pF, +-20ppm, 50Kohms max, SMD
CRY_NX2016SA_4P | Crystal 25MHz, 6pF, +-20ppm, 80ohms max, SMD

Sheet: Project Information
Project Full Path | C:\Users\klomp\Documents\thunderbots\PCB_NucleoClone\NucleoClone.PrjPcb
Project Filename | NucleoClone.PrjPcb
Variant Name | Thunderbots_Clone
Data-Source Filename | NucleoClone.PrjPcb
Data-Source Full Path | C:\Users\klomp\Documents\thunderbots\PCB_NucleoClone\NucleoClone.PrjPcb
Title | Bill of Materials for Variant [Thunderbots_Clone] of Project [NucleoClone.PrjPcb] (No PCB Document Selected)
Total Quantity | 321
Report Time | 14:26
Report Date | 30/11/19
Report Date & Tine | 30/11/19 14:26
Output Name | Bill of Materials
Output Type | BOM_PartType
Output Generator Name | BOM
Output Generator Description | Bill of Materials

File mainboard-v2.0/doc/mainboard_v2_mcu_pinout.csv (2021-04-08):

Position | Name | Type | Signal | Label
1 | PE2 | Output | GPIO_Output | CHARGE_PWR_BRD
2 | PE3 | Input | GPIO_Input | FAULT_PWR_BRD
3 | PE4 | Input | GPIO_Input | DONE_PWR_BRD
4 | PE5 | I/O | GPIO_Analog | HV_SENSE_PWR_BRD
5 | PE6 | Output | GPIO_Output | IMU_INT1
6 | VBAT | Power
7 | PC13 | Output | GPIO_Output | IMU_INT2
8 | PC14-OSC32_IN (OSC32_IN) | I/O | RCC_OSC32_IN | PC14-OSC32_IN
9 | PC15-OSC32_OUT (OSC32_OUT) | I/O | RCC_OSC32_OUT | PC15-OSC32_OUT
10 | PF0 | I/O | I2C2_SDA | IMU_SDA
11 | PF1 | I/O | I2C2_SCL | IMU_SCL
12 | PF2 | Output | GPIO_Output | WHEEL_FRONT_RIGHT_RESET
13 | PF3 | I/O | ADC3_INP5 | ENCODER_FRONT_LEFT_COS
14 | PF4 | I/O | ADC3_INN5 | ENCODER_FRONT_LEFT_SIN
15 | PF5 | I/O | ADC3_INP4 | ENCODER_BACK_LEFT_COS
16 | VSS | Power
17 | VDD | Power
18 | PF6 | I/O | ADC3_INN4 | ENCODER_BACK_LEFT_SIN
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

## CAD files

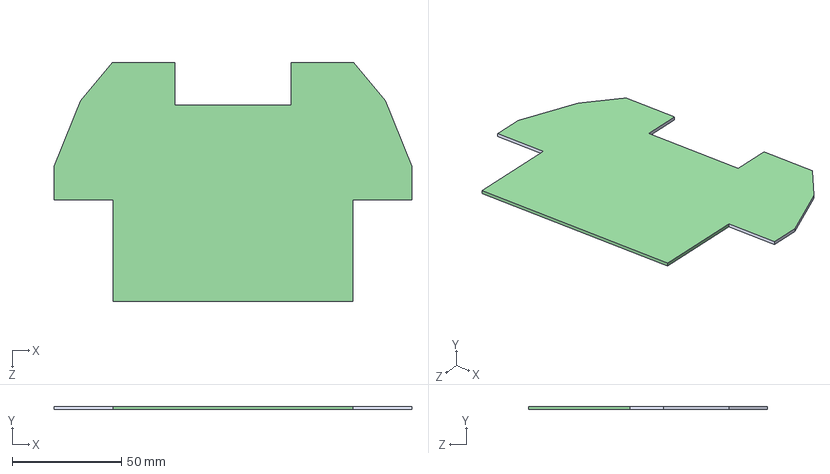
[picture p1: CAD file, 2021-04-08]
mainboard-v2.0/cad/MainBoard_Mock.STEP
164.0 x 1.60 x 109.6 mm

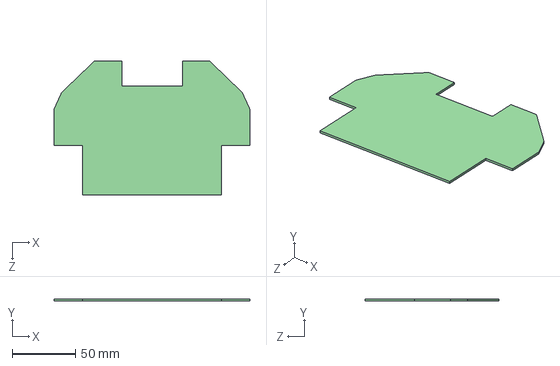
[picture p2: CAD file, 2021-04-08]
mainboard-v2.0/cad/MainBoard_Mock-v2.0.STEP
155.4 x 1.60 x 106.2 mm

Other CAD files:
bob-breakout-v1.1/cad/bobbob-v1.0.x_t

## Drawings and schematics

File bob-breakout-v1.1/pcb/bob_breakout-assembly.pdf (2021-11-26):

1

1

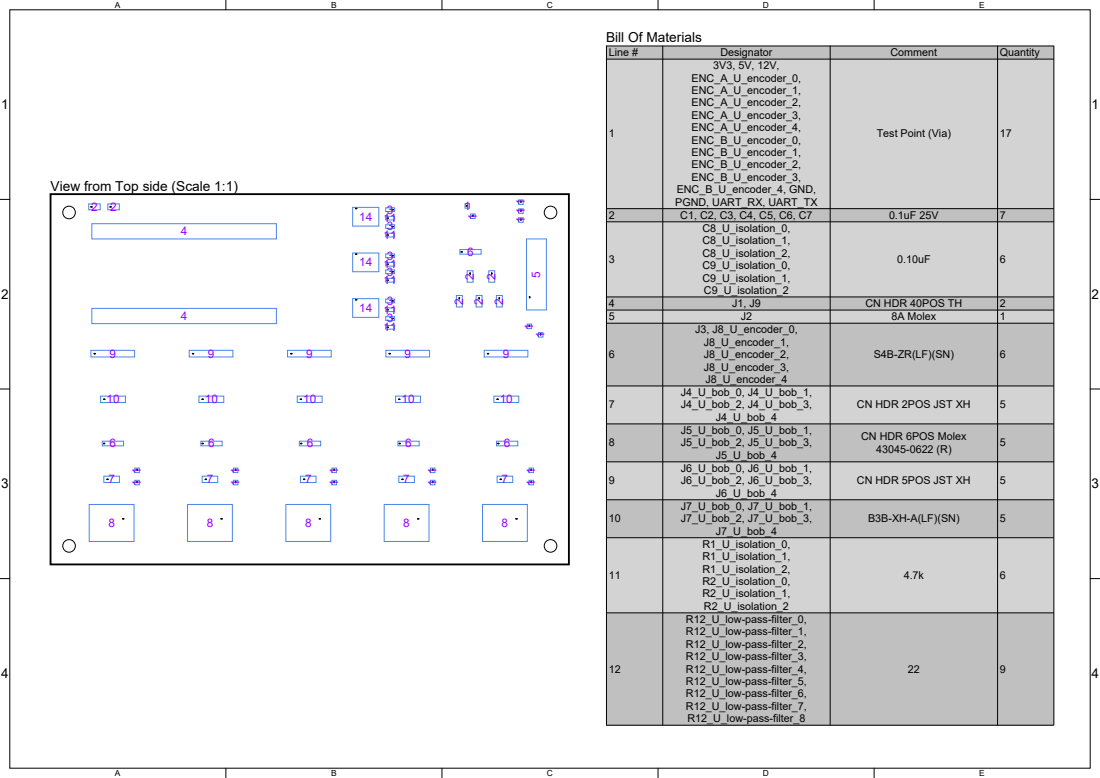
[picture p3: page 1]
Line # 123456789; C1, C2, C3, C4, C5, C6, C7 C8_U_isolation_0, C8_U_isolation_1, C8_U_isolation_2, C9_U_isolation_0, C9_U_isolation_1, C9_U_isolation_2 J1, J9 J2 J3, J8_U_encoder_0, J8_U_encoder_1, J8_U_encoder_2, J8_U_encoder_3, J8_U_encoder_4

Bill Of Materials

Designator | Comment | Quantity

3V3, 5V, 12V, ENC_A_U_encoder_0, ENC_A_U_encoder_1, ENC_A_U_encoder_2, ENC_A_U_encoder_3, ENC_A_U_encoder_4, ENC_B_U_encoder_0, ENC_B_U_encoder_1, ENC_B_U_encoder_2, ENC_B_U_encoder_3, ENC_B_U_encoder_4, GND, PGND, UART_RX, UART_TX | Test Point (Via)

View from Top side (Scale 1:1)

CN HDR 40POS TH
8A Molex

J4_U_bob_0, J4_U_bob_1, J4_U_bob_2, J4_U_bob_3, J4_U_bob_4 | CN HDR 2POS JST XH

J5_U_bob_0, J5_U_bob_1, J5_U_bob_2, J5_U_bob_3, J5_U_bob_4 | CN HDR 6POS Molex 43045-0622 (R)

J6_U_bob_0, J6_U_bob_1, J6_U_bob_2, J6_U_bob_3, J6_U_bob_4 | CN HDR 5POS JST XH

10 | J7_U_bob_0, J7_U_bob_1, J7_U_bob_2, J7_U_bob_3, J7_U_bob_4 | B3B-XH-A(LF)(SN)

11 | R1_U_isolation_0, R1_U_isolation_1, R1_U_isolation_2, R2_U_isolation_0, R2_U_isolation_1, R2_U_isolation_2 | 4.7k

12 | R12_U_low-pass-filter_0, R12_U_low-pass-filter_1, R12_U_low-pass-filter_2, R12_U_low-pass-filter_3, R12_U_low-pass-filter_4, R12_U_low-pass-filter_5, R12_U_low-pass-filter_6, R12_U_low-pass-filter_7, R12_U_low-pass-filter_8 | 22

1 | 1

### View from Bottom side (Scale 1:1)

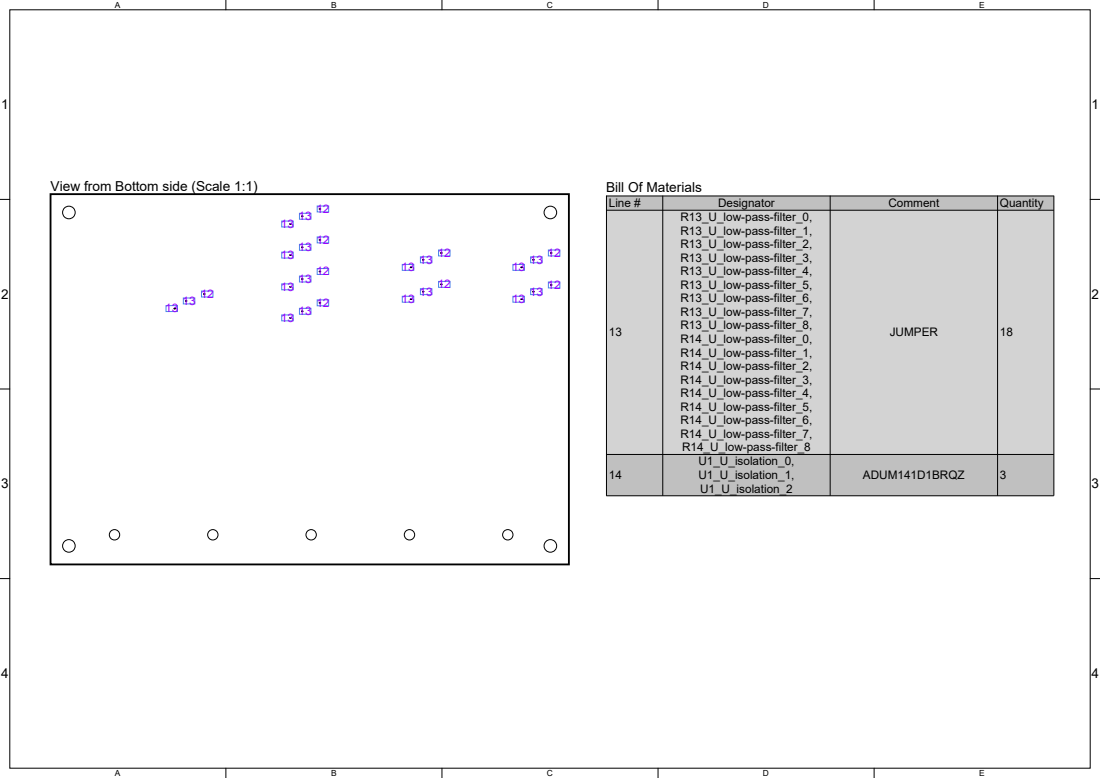
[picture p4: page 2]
Designator R13_U_low-pass-filter_0, R13_U_low-pass-filter_1, R13_U_low-pass-filter_2, R13_U_low-pass-filter_3, R13_U_low-pass-filter_4, R13_U_low-pass-filter_5, R13_U_low-pass-filter_6, R13_U_low-pass-filter_7, R13_U_low-pass-filter_8, R14_U_low-pass-filter_0, R14_U_low-pass-filter_1, R14_U_low-pass-filter_2, R14_U_low-pass-filter_3, R14_U_low-pass-filter_4, R14_U_low-pass-filter_5, R14_U_low-pass-filter_6, R14_U_low-pass-filter_7, R14_U_low-pass-filter_8 U1_U_isolation_0, U1_U_isolation_1, U1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

Bill Of Materials
Line #

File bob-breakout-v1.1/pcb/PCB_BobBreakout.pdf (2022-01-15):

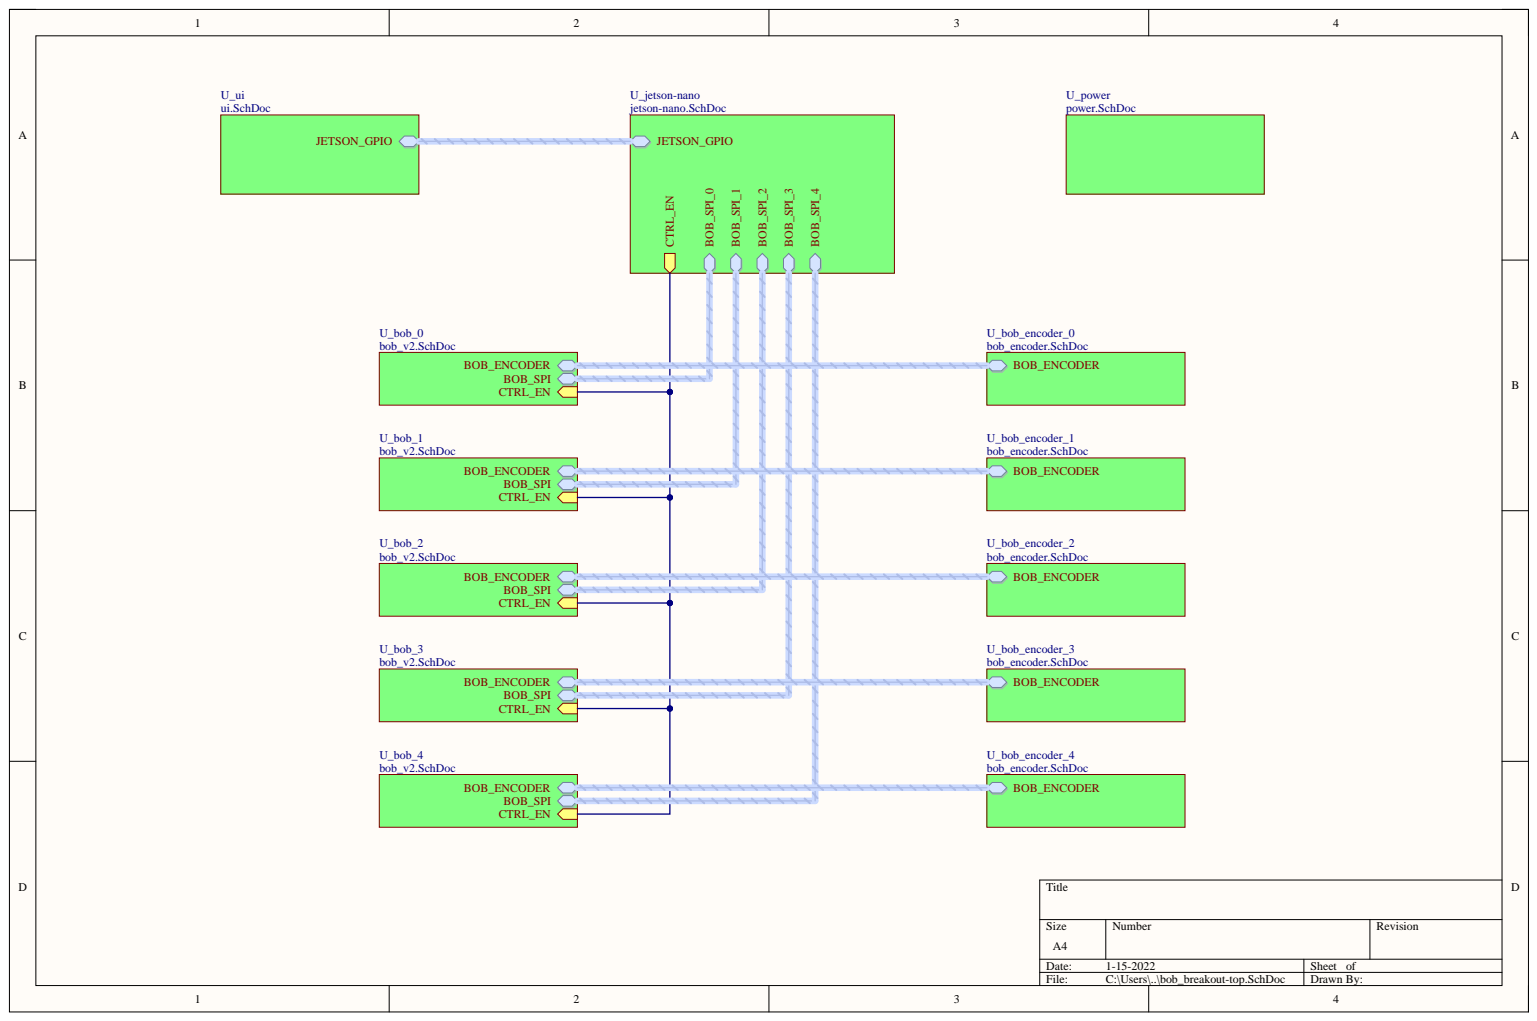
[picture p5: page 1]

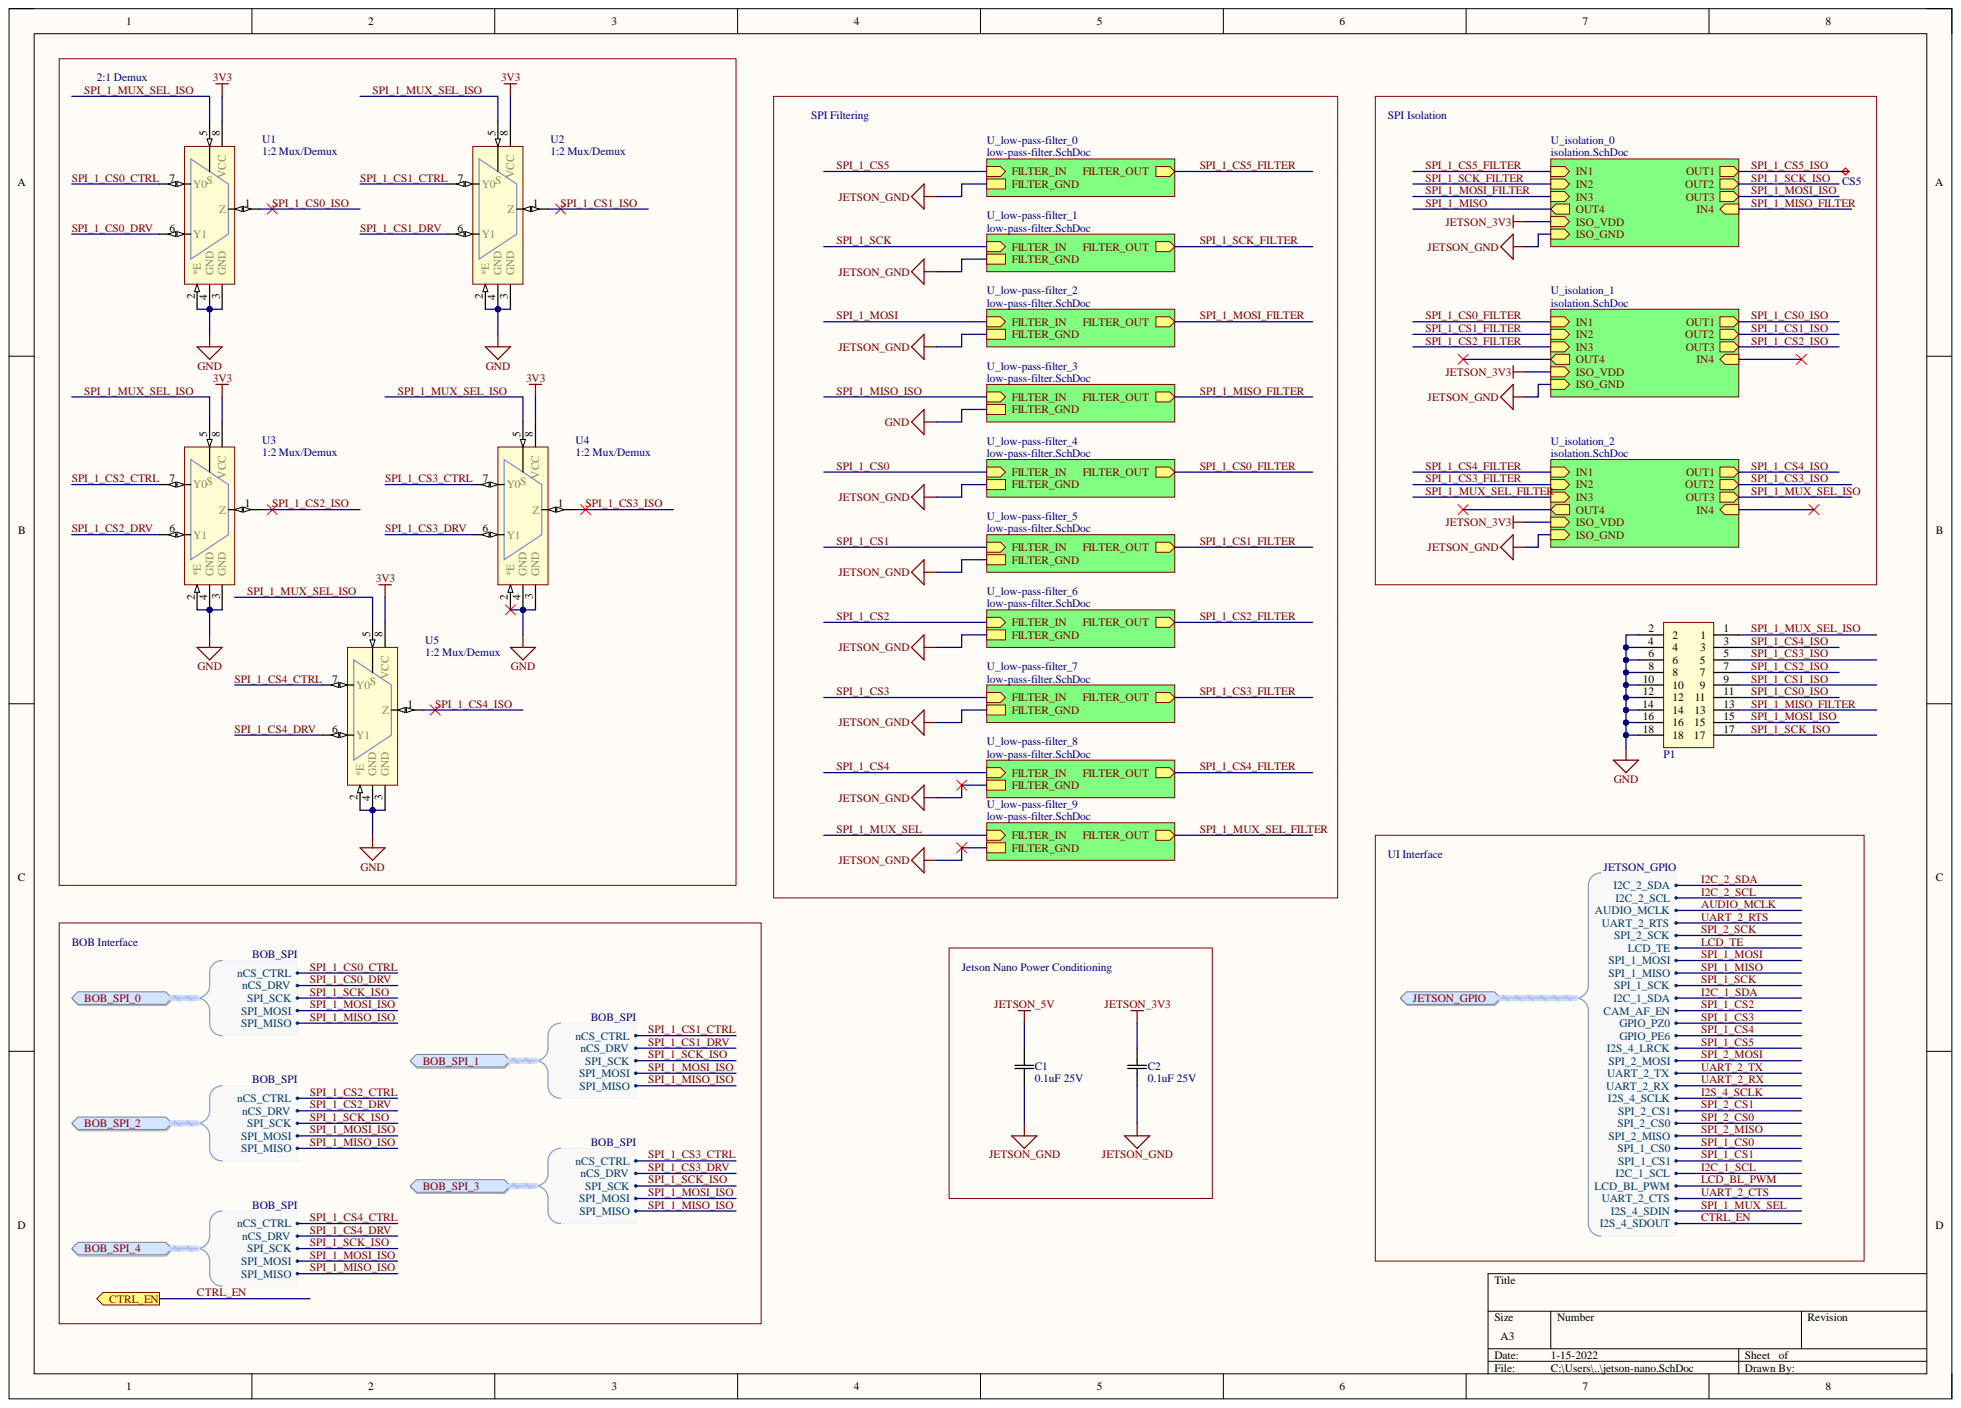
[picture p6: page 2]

Jetson Nano Power Conditioning

VCC1 1 | | OUTA OUTB OUTC IND DIS2

INA 3 | | 14 13 12 11 10

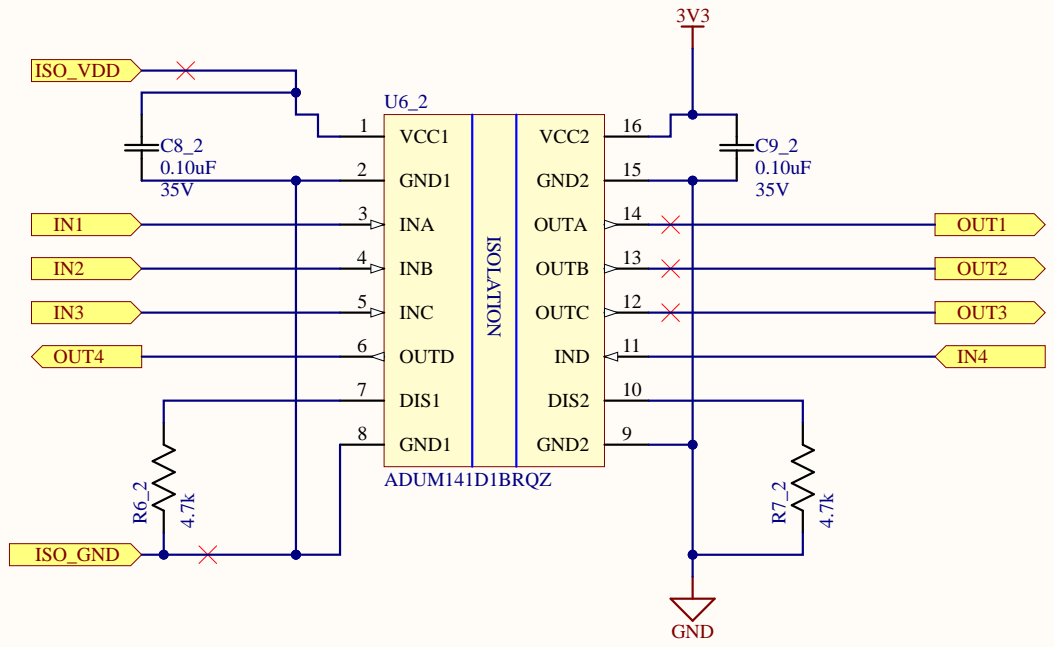
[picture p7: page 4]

VCC1 1 | | OUTA OUTB OUTC IND DIS2

INA 3 | | 14 13 12 11 10

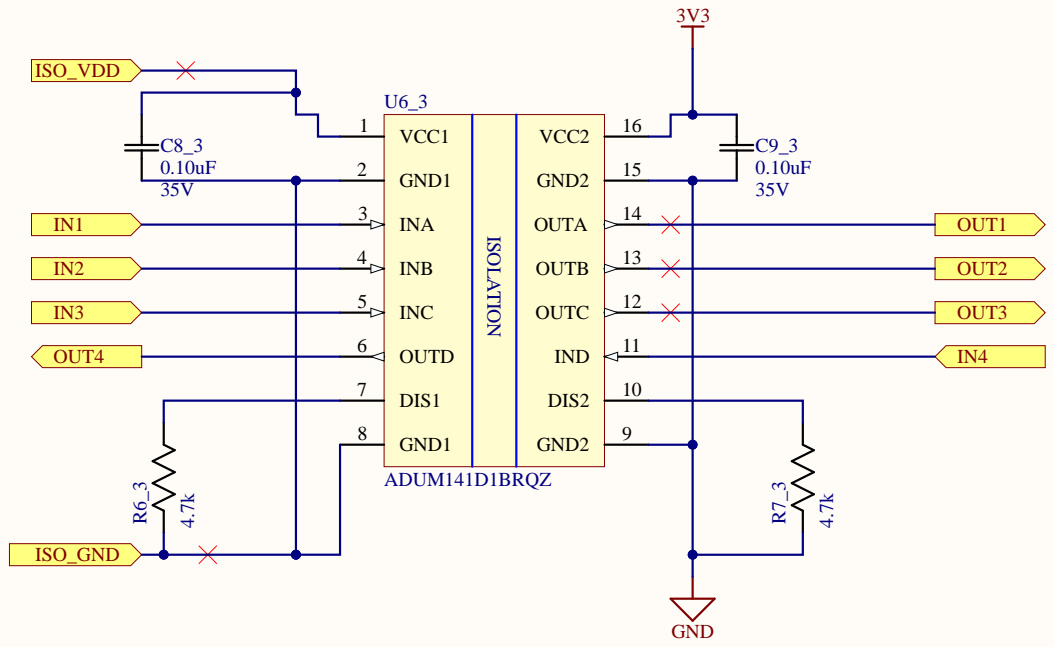
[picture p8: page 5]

VCC1 1 | | OUTA OUTB OUTC IND DIS2

INA 3 | | 14 13 12 11 10

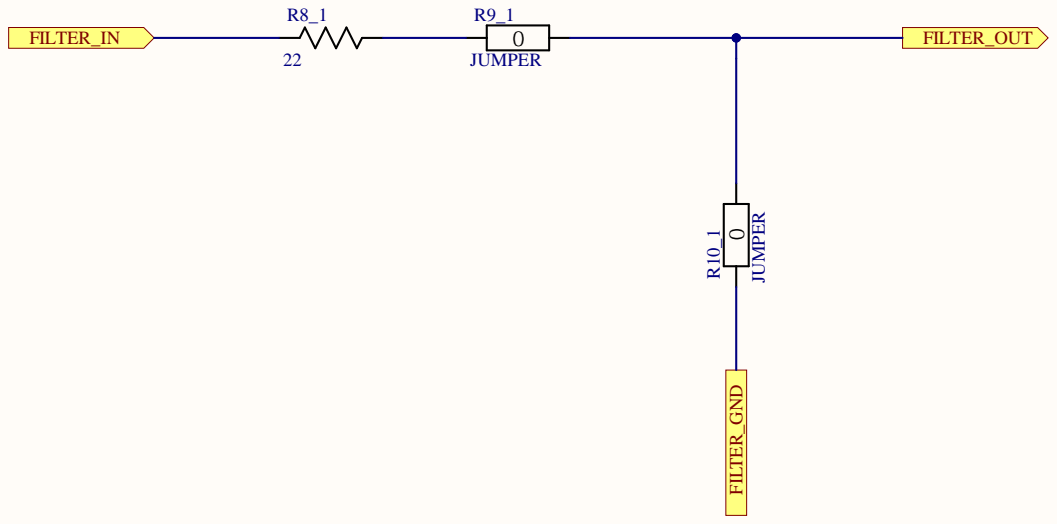
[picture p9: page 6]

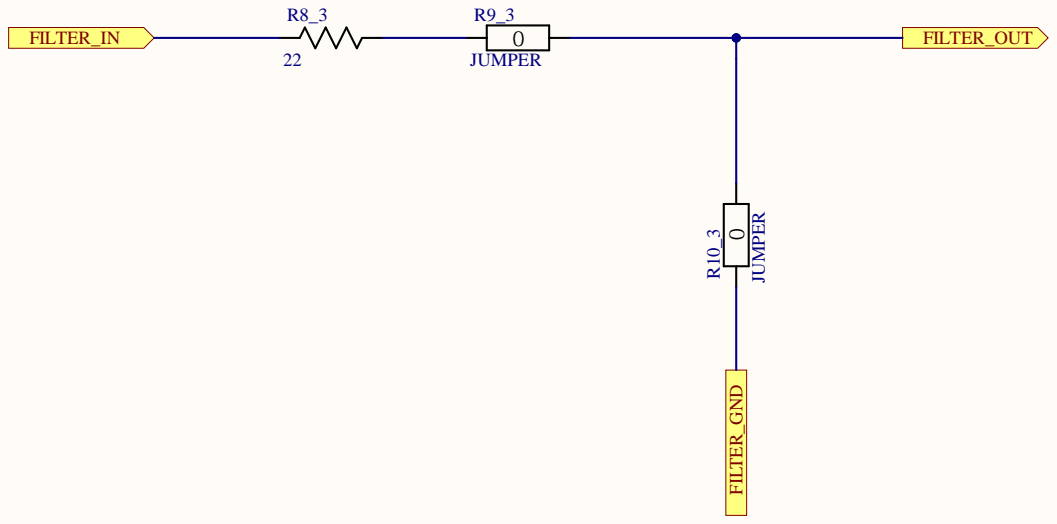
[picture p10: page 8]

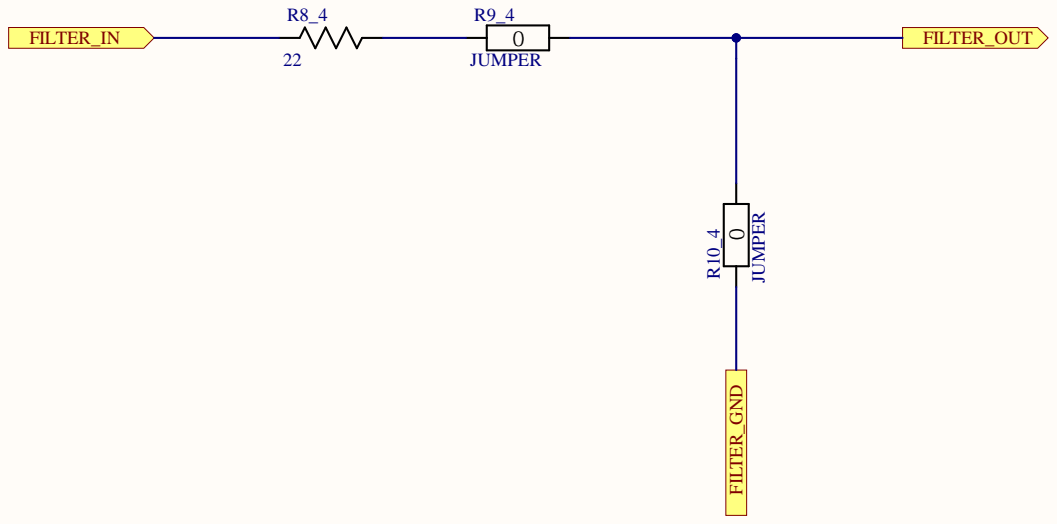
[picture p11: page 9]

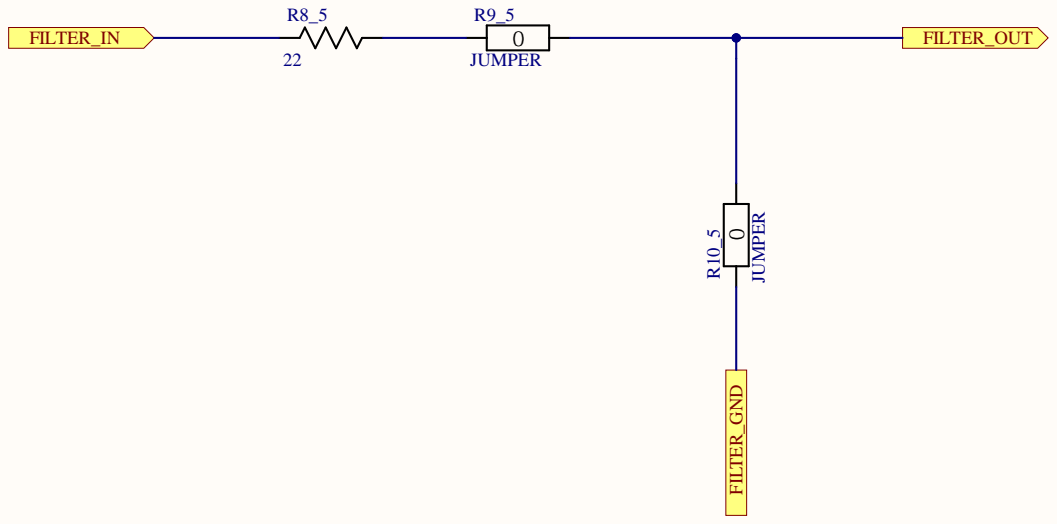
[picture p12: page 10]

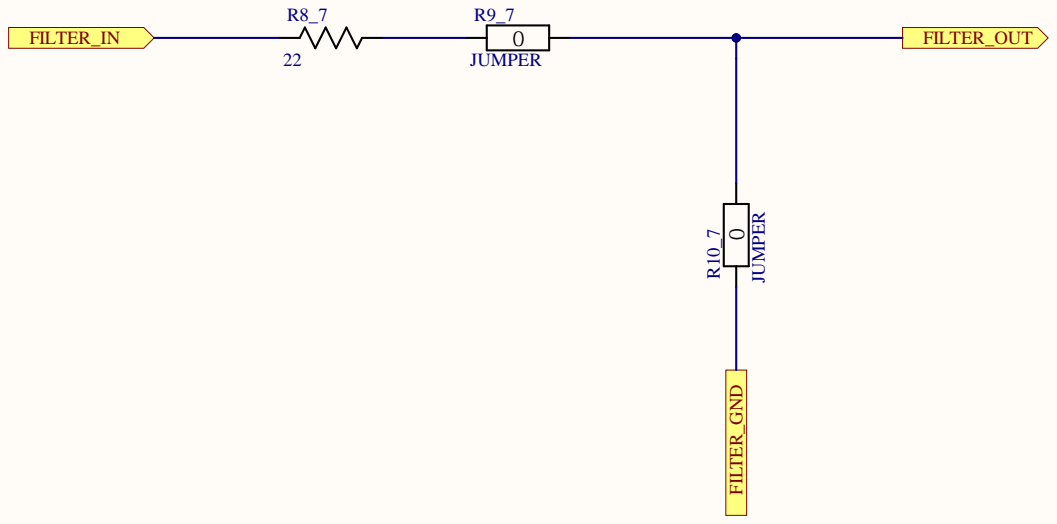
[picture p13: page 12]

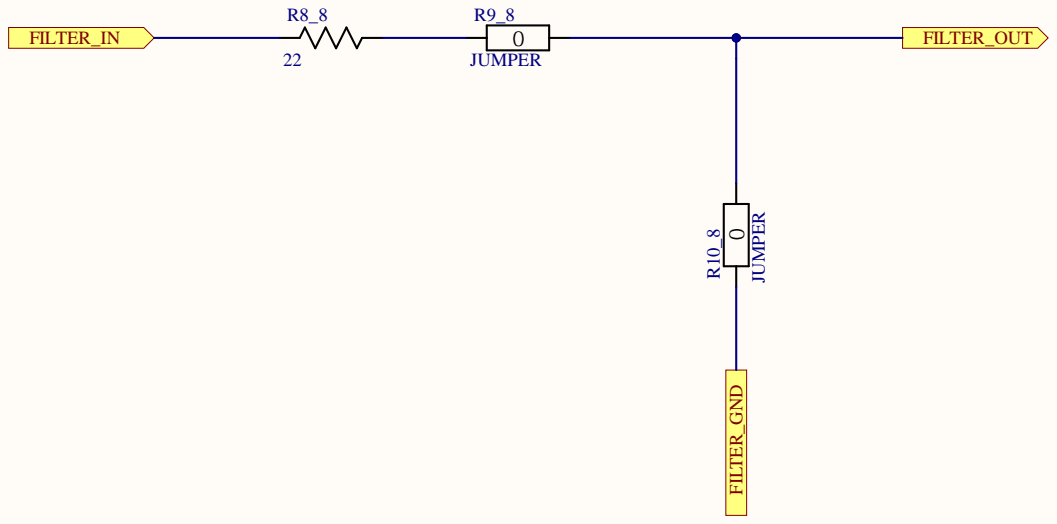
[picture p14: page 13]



~10mA to 15mA through each line













Comment | Description | Designator | Footprint | LibRef | Quantity
Test Point (Via) | | 1, 2, CS5, ENC_A1_1, ENC_A1_2, ENC_A1_3, ENC_A1_4, ENC_A1_5, ENC_B1_1, ENC_B1_2, ENC_B1_3, ENC_B1_4, ENC_B1_5, ENC_N1_1, ENC_N1_2, ENC_N1_3, ENC_N1_4, ENC_N1_5, GND1, VCC1 | TP | Test Point (Via) | 20

0.1uF 25V | CAP CER 0.1UF 25V X7R 0805/0603 | C1, C2, C3, C4, C5, C6, C7 | 0805 | CAP 0.1uF 25V | 7

0.10uF | CAP CER 0.10UF 35V X7R 0603/0805 | C8_1, C8_2, C8_3, C9_1, C9_2, C9_3 | 0603 | CAP 0.10uF 35V | 6

SMAZ12-13-F | Zener Diode 12 V 1 W ±5% Surface Mount SMA | D1 | SMA_DIO-L | DIODE ZENER 12V 1W | 1

LED2 | Typical RED, GREEN, YELLOW, AMBER GaAs LED | D2, D3, D4 | 3.2X1.6X1.1 | LED GREEN SMD | 3

8A Molex | CONN HEADER VERT 10POS 3MM | J1 | MOLEX_0430451012 | CN HDR 10POS MOLEX 0430451012 | 1

CN HDR 40POS TH | SSQ - Samtec 2.54mm Square Tail Dual Row Socket Strip 8.5mm Profile | J2 | SAMTEC_SSQ-120-22-G-D | CN HDR 40POS TH | 1

39299044 | Molex 39299044 4POS Minifit dual row, vertical | J3_1, J3_2, J3_3, J3_4, J3_5 | 39299044 | CN HDR 4POS Molex CN HDR 4POS Molex 39299044 VERT | 5

B5B-ZR(LF)(SN) | Connector Header Through Hole 5 position 0.059 (1.50mm) | J4_1, J4_2, J4_3, J4_4, J4_5 | JST_B5B-ZR(LF)(SN) | CN 5POS JST ZR | 5

CN HDR 18POS 2x9 | | P1 | HDR2x9 | CN HDR 18POS 2x9 | 1
HDR 1x15 | | P2_1, P2_2, P2_3, P2_4, P2_5 | TRINAMIC_BOB | TRINAMIC_BOB | 5

IPB80P03P4L-04 | P-Channel 30 V 80A (Tc) 137W (Tc) Surface Mount PG-TO263-3-2 | Q1 | IPB80P03P4L04 | MOSFET IPB80P03P4L-04 | 1

47k | RES SMD 47k OHM 5% 1/8W 0805 | R1 | 0603 | RES 47k 1/8W - 5% | 1

100k | RES SMD 100K OHM 5% 1/8W 0805/0603 | R2 | 0603 | RES 100k 1/8W - 5% | 1

110 | RES SMD 110 OHM 1% 1/8W 0805/0603 | R3 | 0603 | RES 110.0 1/8W - 1% | 1

330 | RES SMD 330 OHM 5% 1/8W 0805 | R4 | 0603 | RES 330.0 1/8W - 5% | 1

1.96K | RES SMD 1.96K OHM 1% 1/8W 0805 | R5 | 0603 | RES 1.96k 1/8W | 1

4.7k | RES SMD 4.7k OHM 5% 1/8W 0805 | R6_1, R6_2, R6_3, R7_1, R7_2, R7_3 | 0603 | RES 4.7k 1/8W - 5% | 6

22 | RES SMD 22 OHM 5% 1/8W 0805 | R8_1, R8_2, R8_3, R8_4, R8_5, R8_6, R8_7, R8_8, R8_9, R8_10 | 0805 | RES 22.0 1/8W | 10

JUMPER | RES SMD 0 OHM JUMPER GENERIC 0805/0603 | R9_1, R9_2, R9_3, R9_4, R9_5, R9_6, R9_7, R9_8, R9_9, R9_10, R10_1, R10_2, R10_3, R10_4, R10_5, R10_6, R10_7, R10_8, R10_9, R10_10 | 0805 | RES 0 JUMPER | 20

SPST 8.5A 125V | SWITCH SLIDE SPST 8.5A 125V | S1 | SPST GF-123-0054 | SW SLIDE | 1

1:2 Mux/Demux | 74LVC Series 5.5 V SMT 2-Channel Analog Multiplexer/Demultipl exer - TSSOP-8 | U1, U2, U3, U4, U5 | TSOP65P400X110-8N | 74LVC1G53DP,125 | 5

ADUM141D1BRQZ | Digital Isolator CMOS 4-CH 150Mbps 16-Pin QSOP T/R | U6_1, U6_2, U6_3 | SOP64P600X175-16N | ISO ADUM141D1BRQZ | 3

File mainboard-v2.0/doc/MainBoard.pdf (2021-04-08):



ACCELEROMETER, GYROSCOPE, THERMOMETER + OTHER SENSORS

Place capacitor
close to MCU pad


Battery voltage for the
motordrivers.

KICK/CHIP_PWR_BRD logic
levelsignals. Send to MCU.

CHARGE/FAULT/DONE 3.3V logic
signals. From charge control IC. Send to
MCU.

PMS_ALERT_PWR_BRD logic
level fault pin. Send to MCU.

PMS_SDA/SCL I2C communication
wires. Send to MCU.

HV_SENSE analog feedback
from the cap bank voltage
(0-3.3V). Send to MCU.


Diff Pair EMI Filter

1 7 | 2 0 | RD _P | 6 | 1 1 | 3
1 8 | 2 3
8 | 2 2 | | 7 | 1 0 | 5

------------------------------------------ nINTSELF = 0 LED Output = Active High External pull-down resisitor for LE


Size A | Nu m b er | Revisio n

Date: --1 | Sheet o f
File: D:\UB C -Th u n der b ots\..\Main b oar d _Ther | mDr istoawn rAm Bpy.Sch : Do c


CONN MICRO SD CARD PUSH-PUSH R/A



100nF 50V | CAP CER 0.1UF 50V X7R 0805 | C2, C3, C11, C13, C15, C16, C17, C18, C19, C20, C21, C22, C23, C24, C27, C28, C29, C30, C33, C34, C35, C36, C39, C41, C42, C43, C45, C46, C66 | | | 0805 | CAP 100nF 50V | | | 0805 | | 29 100nF

1uF 50V | CAP CER 1UF 50V X7R 0805 | C4, C9, C10, C12, C38, C49 | | | 0805 | CAP 1uF 50V | | | 0805 | | 6 1uF

2.2uF | CAP CER 2.2UF 35V X7R 0603/0805 | C5, C7, C8 | | | 0805 | CAP 2.2uF 35V | | | 0603/0805 | | 3 2.2uF

470pF | CAP CER 470PF 50V X7R 0603/0805 | C6, C40 | | | 0805 | CAP 470pF 50V | | | 0603/0805 | | 2 470pF

4.7uF | CAP CER 4.7UF 35V X7R 0603/0805 | C14 | | | 0805 | CAP 4.7uF 35V | | | 0603/0805 | | 1 4.7uF

0.010uF | CAP CER 0.010UF 50V X7R 0603/0805 | C25, C26, C31, C32, C37 | | | 0805 | CAP 0.010uF 50V | | | 0603/0805 | | 5 0.010uF

10uF 10V | CAP TANT 10UF 10V 1206 | C44 | | | 1206 Polarized | CAP TANT 10uF 10V | | | 1206 | | 1 10uF

30pF 25V | CAP CER 30PF 25V NP0 0805 | C47, C50 | | | 0805 | CAP 30pF 25V | | | 0805 | | 2 30pF

1000pF | CAP CER 1000PF 50V X7R 0603/0805 | C48 | | | 0603 | CAP 1000pF 50V | | | 0603/0805 | | 1 1000pF

CAP POL 0.1uF 100V | 0.1µF 100V Aluminum Electrolytic Capacitors, Through-Hole, Radial, Can 2000 Hrs @ 85°C | C51, C52, C53, C54, C55, C56, C57, C58, C59, C60, C61, C62, C63, C64, C65 | | | CAPPRD200W50D 525H1250 | CAP POL 0.1uF 100V | | | | | 15 0.10uF

5.6uF | CAP CER 5.6UF 6.3V X5R 0805 | C67, C69 | | | 0805 | CAP 5.6uF 6.3V | | | 0805 | | 2 5.6uF

5.1pF 630V | CAP CER 5.1PF 630V C0G/NP0 0805 | C68, C70 | | | 0805 | CAP 5.1pF 630V | | | 0805 | | 2 5.1pF

0.10uF | CAP CER 0.10UF 16V X5R 0603/0805 | C71 | | | 0603 | CAP 0.10uF 16V | | | 0603/0805 | | 1 0.10uF

2.8V | Zener Diode 2.8V 500mW ±5% Surface Mount SOD-123 | D1 | | | SOD-123 | DIODE ZENER 2.8V 500mW | | | | | 1

SM5817PL-TP | Diode Schottky 20V 1A Surface Mount SOD-123FL | D2, D3, D4, D5 | SM5817PL-TPMSCT-ND | https://www.digikey.ca/product-detail/en/micro-commercial-co/SM5817PL-TP/SM5817PL-TPMSCT-ND/1793410 | SOD-123 | DIODE SCHOTTKY 20V 1A | Micro Commercial Co | SM5817PL-TP | SOD-123 | | 4

APHF1608SEEQBD ZGKC | Red, Green, Blue (RGB) 621nm Red, 525nm Green, 465nm Blue LED Indication -Discrete 2V Red, 3.3V Green, 3.3V Blue 4-SMD, No Lead | D6 | 754-2144-1-ND | | LED RGB APHF1608SEEQBD ZGKC_KNB-L | LED RGB CLEAR 4SMD | Kingbright | APHF1608SEEQBD ZGKC | | | 1

LED2 | Typical RED, GREEN, YELLOW, AMBER GaAs LED | Dled1, Dled2, Dled3, Dled4, Dusr1, Dusr2 | | | 3.2X1.6X1.1 | LED GREEN SMD, LED RED SMD | | | 1206 | | 6

Fuse 3A 1206 | FUSE 3A 63V AC/DC SLOW 1206 F1 | | | | 1206 | FUSE 3A 63V SLOW | | | | | 1

1.5mm | Conn Shrouded Header HDR 6 POS 1.5mm Solder RA Thru-Hole Box | J1, J2, J3, J4 | | | 6POS JST | CN 6POS JST RA | | | | | 4

CN J00-0045NL | CN MAGJACK 1PORT 100 BASE-TX | J5 | 553-1619-5-ND | https://www.digikey.com/product-detail/en/pulse-electronics-network/J00-0045NL/553-1619-5-ND/1036860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 | RJ45 J00-0045NL | CN MAGJACK | Pulse Electronics | J00-0045NL | None | | 1

0.1" Header Female 34 | Female Header THRU 34POS 2ROW 0.1" (2.54mm) pitch | J6 | | | SAMTEC-SSM-117-X-DV | CN HDR 34POS 2x17 | | | | | 1

CN PCIE 36 TH | 36 Position Female Connector PCI Expressâ„¢ Gold 0.039 _1.00mm_ Black 10018784-10210TLF | J7, J8, J9, J10, J11 | | | CN PCIE 36 TH | CN PCIE 36 TH | Amphenol ICC | 10018784-10210TLF | None | None | 5
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

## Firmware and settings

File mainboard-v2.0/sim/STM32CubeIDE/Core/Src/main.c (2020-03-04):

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

/* Includes ------------------------------------------------------------------*/
#include "main.h"
#include "string.h"

#if defined ( __ICCARM__ ) /*!< IAR Compiler */

#pragma location=0x30040000
ETH_DMADescTypeDef  DMARxDscrTab[ETH_RX_DESC_CNT]; /* Ethernet Rx DMA Descriptors */
#pragma location=0x30040060
ETH_DMADescTypeDef  DMATxDscrTab[ETH_TX_DESC_CNT]; /* Ethernet Tx DMA Descriptors */
#pragma location=0x30040200
uint8_t Rx_Buff[ETH_RX_DESC_CNT][ETH_MAX_PACKET_SIZE]; /* Ethernet Receive Buffers */

#elif defined ( __CC_ARM )  /* MDK ARM Compiler */

__attribute__((at(0x30040000))) ETH_DMADescTypeDef  DMARxDscrTab[ETH_RX_DESC_CNT]; /* Ethernet Rx DMA Descriptors */
__attribute__((at(0x30040060))) ETH_DMADescTypeDef  DMATxDscrTab[ETH_TX_DESC_CNT]; /* Ethernet Tx DMA Descriptors */
__attribute__((at(0x30040200))) uint8_t Rx_Buff[ETH_RX_DESC_CNT][ETH_MAX_PACKET_SIZE]; /* Ethernet Receive Buffer */

#elif defined ( __GNUC__ ) /* GNU Compiler */ 

ETH_DMADescTypeDef DMARxDscrTab[ETH_RX_DESC_CNT] __attribute__((section(".RxDecripSection"))); /* Ethernet Rx DMA Descriptors */
ETH_DMADescTypeDef DMATxDscrTab[ETH_TX_DESC_CNT] __attribute__((section(".TxDecripSection")));   /* Ethernet Tx DMA Descriptors */
uint8_t Rx_Buff[ETH_RX_DESC_CNT][ETH_MAX_PACKET_SIZE] __attribute__((section(".RxArraySection"))); /* Ethernet Receive Buffers */

#endif

ETH_TxPacketConfig TxConfig; 
ADC_HandleTypeDef hadc1;
ADC_HandleTypeDef hadc2;
ADC_HandleTypeDef hadc3;

ETH_HandleTypeDef heth;

I2C_HandleTypeDef hi2c1;
I2C_HandleTypeDef hi2c2;

SPI_HandleTypeDef hspi1;

TIM_HandleTypeDef htim2;
TIM_HandleTypeDef htim3;
TIM_HandleTypeDef htim4;
TIM_HandleTypeDef htim5;

void SystemClock_Config(void);
static void MX_GPIO_Init(void);
static void MX_ADC1_Init(void);
static void MX_ADC2_Init(void);
static void MX_ADC3_Init(void);
static void MX_ETH_Init(void);
static void MX_I2C1_Init(void);
static void MX_I2C2_Init(void);
static void MX_SPI1_Init(void);
static void MX_TIM2_Init(void);
static void MX_TIM3_Init(void);
static void MX_TIM4_Init(void);
static void MX_TIM5_Init(void);
/* USER CODE BEGIN 0 */
#define SYSCLOCK 64000000 // System Clock is 64MHz
/* USER CODE END 0 */

/**
  * @brief  The application entry point.
  * @retval int
  */
int main(void)
{
  

  /* Enable I-Cache---------------------------------------------------------*/
  SCB_EnableICache();

  /* Enable D-Cache---------------------------------------------------------*/
  SCB_EnableDCache();

  /* MCU Configuration--------------------------------------------------------*/

  /* Reset of all peripherals, Initializes the Flash interface and the Systick. */
  HAL_Init();

  /* Configure the system clock */
  SystemClock_Config();

  /* Initialize all configured peripherals */
  MX_GPIO_Init();
  MX_ADC1_Init();
  MX_ADC2_Init();
  MX_ADC3_Init();
  MX_ETH_Init();
  MX_I2C1_Init();
  MX_I2C2_Init();
  MX_SPI1_Init();
  MX_TIM2_Init();
  MX_TIM3_Init();
  MX_TIM4_Init();
  MX_TIM5_Init();
  /* USER CODE BEGIN 2 */
  // Code to Initialize TIMERS
  // HAL_TIM_PWM_Init(&htim2);
  //if (HAL_TIM_PWM_ConfigChannel(&htim2, &sConfigOC, TIM_CHANNEL_1) != HAL_OK)
  //  {
  //    Error_Handler();
  //  }
  if (HAL_TIM_Base_Start(&htim2) != HAL_OK) {
	  Error_Handler();
  }
  if (HAL_TIM_PWM_Start(&htim2, TIM_CHANNEL_1) != HAL_OK) {
	  // Error Starting PWM
	  Error_Handler();
  }
  if (HAL_TIM_PWM_Start(&htim2, TIM_CHANNEL_3) != HAL_OK) {
  	  // Error Starting PWM
  	  Error_Handler();
  }
  if (HAL_TIM_Base_Start(&htim4) != HAL_OK) {
  	  Error_Handler();
  }
  if (HAL_TIM_PWM_Start(&htim4, TIM_CHANNEL_1) != HAL_OK) {
	  // Error Starting PWM
	  Error_Handler();
  }
  if (HAL_TIM_PWM_Start(&htim4, TIM_CHANNEL_2) != HAL_OK) {
	  // Error Starting PWM
	  Error_Handler();
  }
  /* USER CODE END 2 */
 
 

  /* Infinite loop */
  /* USER CODE BEGIN WHILE */
  while (1)
  {
    /* USER CODE END WHILE */

    /* USER CODE BEGIN 3 */
  }
  /* USER CODE END 3 */
}

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


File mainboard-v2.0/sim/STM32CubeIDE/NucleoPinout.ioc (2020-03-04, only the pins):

Mcu.UserName=STM32H743ZITx
PA0.Signal=S_TIM5_CH1
PA1.Signal=ETH_REF_CLK
PA10.Signal=GPIO_Output
PA11.Signal=GPIO_Input
PA2.Signal=ETH_MDIO
PA5.Signal=S_TIM2_CH1
PA6.Signal=ADCx_INP3
PA7.Signal=ETH_CRS_DV
PA8.Signal=GPIO_Output
PA9.Signal=GPIO_Output
PB1.Signal=ADCx_INP5
PB10.Signal=S_TIM2_CH3
PB11.Signal=ETH_TX_EN
PB12.Signal=ETH_TXD0
PB13.Signal=ETH_TXD1
PB14.Signal=GPIO_Output
PB15.Signal=GPIO_Input
PB6.Signal=I2C1_SCL
PB7.Signal=I2C1_SDA
PC1.Signal=ETH_MDC
PC11.Signal=GPIO_Output
PC12.Signal=GPIO_Output
PC3_C.Signal=ADC3_INP1
PC4.Signal=ETH_RXD0
PC5.Signal=ETH_RXD1
PC6.Signal=S_TIM3_CH1
PC7.Signal=S_TIM3_CH2
PC8.Signal=GPIO_Input
PC9.Signal=GPIO_Input
PD10.Signal=GPIO_Output
PD12.Signal=S_TIM4_CH1
PD13.Signal=S_TIM4_CH2
PD15.Signal=GPIO_Input
PD7.Signal=SPI1_MOSI
PD8.Signal=GPIO_Input
PD9.Signal=GPIO_Output
PE1.Signal=GPIO_Output
PE11.Signal=GPIO_Output
PE12.Signal=GPIO_Output
PE13.Signal=GPIO_Input
PE14.Signal=GPIO_Input
PE7.Signal=GPIO_Output
PE8.Signal=GPIO_Input
PF0.Signal=I2C2_SDA
PF1.Signal=I2C2_SCL
PF11.Signal=ADC1_INP2
PF12.Signal=ADC1_INP6
PF13.Signal=ADC2_INP2
PF14.Signal=ADC2_INP6
PF7.Signal=ADC3_INP3
PF9.Signal=ADC3_INP2
PG0.Signal=GPIO_Output
PG1.Signal=GPIO_Output
PG10.Signal=SPI1_NSS
PG11.Signal=SPI1_SCK
PG2.Signal=GPIO_Input
PG3.Signal=GPIO_Output
PG4.Signal=GPIO_Output
PG5.Signal=GPIO_Input
PG6.Signal=GPIO_Input
PG7.Signal=GPIO_Output
PG8.Signal=GPIO_Output
PG9.Signal=SPI1_MISO

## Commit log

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2019-12-20 All features have been added, compiles with errors, need to add pwr leds
    [Connectors_Clone.SchDoc, MCU_144_IOs_Clone.SchDoc, NucleoClone Components.xls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]
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2019-12-29 Still need to add USB pwr option and replace some misc parts with Altium Library equivalents
    [Connectors_Clone.SchDoc, MCU_144_IOs_Clone.SchDoc, MCU_144_POWER_Clone.SchDoc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]
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2019-12-30 Added PCB file, changed some pwr and I/O names
    [Connectors_Clone.SchDoc, MCU_144_IOs_Clone.SchDoc, MCU_144_POWER_Clone.SchDoc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]
2019-12-30 Fixed RMII header
    [Connectors_Clone.SchDoc, MCU_144_IOs_Clone.SchDoc, MCU_144_POWER_Clone.SchDoc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]
2020-01-01 Fixed compile problem
    [Connectors_Clone.SchDoc, MCU_144_IOs_Clone.SchDoc, MCU_144_POWER_Clone.SchDoc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]
2020-01-03 Updated PCB layout, still some existing compile issues where footprints are not found
    [Connectors_Clone.SchDoc, MCU_144_IOs_Clone.SchDoc, MCU_144_POWER_Clone.SchDoc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]
2020-01-03 Swapped out zener for schottky on power
    [Connectors_Clone.SchDoc, MCU_144_IOs_Clone.SchDoc, MCU_144_POWER_Clone.SchDoc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]
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2020-01-17 Only pushing new files, for new main board
    [MainBoard_144_IOs.SchDoc, MainBoard_MCU_PWR.SchDoc, MainBoard_Top.SchDoc]
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2020-03-05 IMU breakout and small changes that come from saving in altium simply
    [IMU_Breakout.PcbDoc, IMU_Breakout.PrjPCB, IMU_breakout.SchDoc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]
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2020-11-16 Reorganized and added to connectors
    Added new "differential to single ended output converter" as encoder connector. Split connector schematic into constituent schematics, reorganized top schematic accordingly.
    [MainBoard.PrjPCB, MainBoard_Connectors.SchDoc, MainBoard_Top.SchDoc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]
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2021-01-09 Split schematics, midway through finagling ports
    Schematics assigned to myself in trello were created and organized, Mainboard_144_IO renamed to Mainboard_MCU_Breakout. Made some new ports but am not sure if they should be kept.
    [MainBoard.PrjPCB, MainBoard_144_IOs.SchDoc, MainBoard_MCUBreakout.SchDoc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]
2021-01-10 Finished adding ports and reorganized Top Sch
    Ports all added, top schematic reorganized, still need to make sure I didnt miss any ports / do any ports wrong
    [MainBoard_MCUBreakout.SchDoc, MainBoard_Top.SchDoc, Mainboard_MCUFunc.SchDoc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]
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2021-01-12 Updated power board connector and renamed several schematics.
    [MainBoard_MCU_Breakout.SchDoc, Mainboard_Encoder_Interface.SchDoc, Mainboard_Ethernet.SchDoc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]
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2021-01-12 Copied rmii interface from rmii dongle into RMII_Interface, tidied up Mainboard_Top.
    [MainBoard.PrjPCB, MainBoard_MCUPwr.SchDoc, MainBoard_MCU_Power.SchDoc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]
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2021-01-14 Completed User Intereface Schematic and organized/migrated other schematics into specified boards
    [MainBoard.PrjPCB, MainBoard_144_IOs.SchDoc, MainBoard_MCU_PWR.SchDoc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]
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2021-01-24 Created User_Interface_Schematic and linked compenents in the schematic
    [MainBoard.PrjPCB, Mainboard_MCU_Breakout.SchDoc, Mainboard_Wifi_Interface.SchDoc]
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2021-01-25 Removed USB and added STLINK connections to MCU_Breakout.
    [MainBoard.PrjPCB, MainBoard_MCU_Breakout.SchDoc, MainBoard_Top.SchDoc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]
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2021-01-26 Fixed MCU_Breakout ghost file bug.
    [MainBoard.PrjPCB, MainBoard_MCU_Breakout.SchDoc, MainBoard_Top.SchDoc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]
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2021-01-26 Updated repository structure and mapped port connections to MCU.
    [MainBoard_Layout_V2.PcbDoc, MainBoard_MCU_Power.SchDoc, MainBoard_Top.SchDoc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]
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2021-01-27 replaced ceramic capacitors in Motordriver_Interface with electrolytic
    [Mainboard_Motordriver_Interface.SchDoc]
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2021-01-31 linked (hopefully) all the components to footprints in AL, added working-dannon pcbDoc
    [MainBoard.PrjPCB, MainBoard_MCU_Power.SchDoc, Mainboard_Encoder_Interface.SchDoc]
2021-01-31 forgot to commit the project file and sending most updated MCU_power schematic
    [MainBoard.PrjPCB, MainBoard_MCU_Power.SchDoc]
2021-01-31 added proper values to filter resistors in Encoder_Interface as per Dominic's reference sheet
    [Mainboard_Encoder_Interface.SchDoc]
2021-02-05 Updated SD Card and RGB LED components; Completed RMII_Interface component layout.
    [MainBoard.PrjPCB, Mainboard_Encoder_Interface.SchDoc, Mainboard_RMII_Interface.SchDoc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]
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2021-02-06 created new working branch, did motor driver interface layout
    [MainBoard.PrjPCB]
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2021-02-08 Finalized board shape, standoff locations, and power board connector.
    [MainBoard.PrjPCB, Mainboard_ThermistorAmp.SchDoc]
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2021-02-13 did layout for motor driver interface, added vias to 5V, 3V3 nets
    [MainBoard.PrjPCB]
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2021-02-13 changed polygon to relief connect, replaced polys with direct traces
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2021-02-13 Made it so that changes exist in new file
    [MainBoard.PrjPCB]
2021-02-13 fixed layout, added trace to power interface
2021-02-14 moved mainboard layout v1 file to correct folder.
    [MainBoard_Layout_V1.PcbDoc]
2021-02-14 User_Interface_Route_V1
    Finished internal routing within the user interface room and inserts VIA's where I felt comfortable to reach other parts of the board
    [MainBoard.PrjPCB, Mainboard_MCU_Func.SchDoc]
2021-02-14 Rerouted rmii dongle section and added nucleo design files to _archive.
    [Connectors.SchDoc, Ethernet.SchDoc, MB1364.PrjPcb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]
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2021-02-14 Updated MCU power schematics and cleaned up some traces.
    [MainBoard_MCU_Power.SchDoc]
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2021-02-18 Routed RMII and IMU cross-board connections. Added global 3V3 polygon.
    [Mainboard_Encoder_Interface.SchDoc]
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2021-02-25 Improved 3V3 power delivery, fixed most of silkscreen
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2021-02-26 3v3ified the breakbeam, finished fixing silkscreen
    [Mainboard_Breakbeam_Interface.SchDoc]
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2021-03-01 Updated digikey part number on components, created BOM and Gerber output jobs.
    [MainBoard.PrjPCB, MainBoard_MCU_Power.SchDoc, MainBoard_Top.SchDoc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]
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2021-03-04 Updated output jobs for JLC and Digikey order.
    [MainBoard.PrjPCB, MainBoard_MCU_Power.SchDoc, Mainboard_ThermistorAmp.SchDoc]
2021-03-04 User_Interface routing (without one piano switch and breakbeam)
    User_Interface routing (without one piano switch and breakbeam)
    [MainBoard.PrjPCB]
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2021-03-06 Changed GND polygon and board size to accomodate capacitors, added stiching vias to RMII transformer.
    [MainBoard.PrjPCB]
2021-03-06 Fixed general routing issues, moved thermistor off board (temp).
    [MainBoard_MCU_Power.SchDoc, Mainboard_Encoder_Interface.SchDoc, Mainboard_MCU_Breakout.SchDoc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]
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2021-03-13 Altered MCU Power Sch, file cleanup into _archive
    [MB1364.PrjPcb, MainBoard.PrjPCB, MainBoard_MCU_Power.SchDoc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]
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2021-03-14 Added gnd shield under PHY oscillator
2021-03-14 Added GND connections to missing components.
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2021-03-21 Routed Geneva + missing connections
    [MainBoard.PrjPCB, MainBoard_MCU_Power.SchDoc, MainBoard_Top.SchDoc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]
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2021-03-24 Mainboard 2.0 with piezo buzzer
    [MainBoard.PrjPCB]
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2021-03-25 Replaced 3V3 power select diodes with jumpers, 5VUSB diode added
    [MainBoard_MCU_Power.SchDoc, Mainboard_Wifi_Interface.SchDoc]
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2021-10-26 fixed duplicate net issue
    [PCB_BobBreakout.PrjPcb, bob_breakout-top.SchDoc, bob_breakout-v1.0.SchDoc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]
2021-10-27 fixed component layout bugs
    [bob_breakout.PcbDoc]
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2021-10-29 fixed motordriver spi cs pin bug
    [PCB_BobBreakout.PrjPcb, jetson-nano.SchDoc, layout.PcbDoc]
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2021-12-16 trying to add stitching
    If there are Polygons or Fills on other nets that are overlapping within that area (on another layer), stitching is not applied in that region. (UGHHHH)
    [PCB_BobBreakout.PrjPcb, bob_breakout-layout.PcbDoc, bob_v2.SchDoc]
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2021-12-19 changed orientation of motor connectors near BOBs so that the tab faces away from the BOBs
    [bob_breakout-layout.PcbDoc]
2021-12-19 shifted P2_1 and P2_3 over to give more space for the motor connectors
    [bob_breakout-layout.PcbDoc]
2021-12-19 fixed some silkscreen
    [bob_breakout-layout.PcbDoc]
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

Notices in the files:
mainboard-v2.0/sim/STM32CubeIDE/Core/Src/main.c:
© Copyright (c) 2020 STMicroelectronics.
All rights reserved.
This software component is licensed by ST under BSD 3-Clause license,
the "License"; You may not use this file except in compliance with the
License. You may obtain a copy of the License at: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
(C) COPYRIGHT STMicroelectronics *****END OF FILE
